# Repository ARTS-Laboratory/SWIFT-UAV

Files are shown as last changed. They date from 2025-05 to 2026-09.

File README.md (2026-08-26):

# Scientific Workhorse for In-flight Field Tests – UAV (SWIFT-UAV)

Repository for the open-source SWIFT-UAV being developed at the University of South Carolina. 

<p align="center">
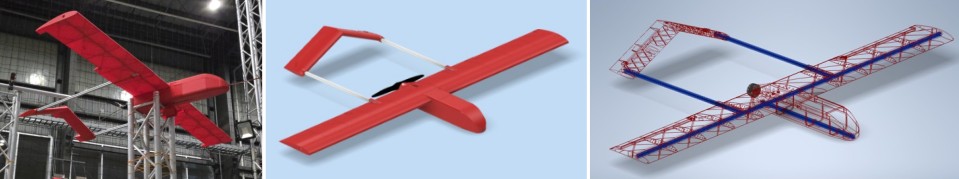
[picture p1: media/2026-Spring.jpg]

</p>
<p align="center">
The SWIFT UAV (Pelican V0.3) in Spring 2026.
</p>

## Licensing and Citation

[][cc-by-sa]

This work is licensed under a
[Creative Commons Attribution-ShareAlike 4.0 International License][cc-by-sa].

[cc-by-sa]: http://creativecommons.org/licenses/by-sa/4.0/
[cc-by-sa-image]: https://licensebuttons.net/l/by-sa/4.0/88x31.png
[cc-by-sa-shield]: https://img.shields.io/badge/License-CC%20BY--SA%204.0-lightgrey.svg

Cite as:

@Misc{ARTSLabSwiftUavScientific,     
  author = {{ARTS-L}ab},  
  howpublished = {GitHub},    
  title  = {SWIFT-UAV: Scientific Workhorse for In-flight Field Tests – UAV},    
  groups = {{ARTS-L}ab},    
  url    = {https://github.com/ARTS-Laboratory/SWIFT-UAV},   
  note        = {Accessed: Month dd, yyyy},   
}

<p align="center">
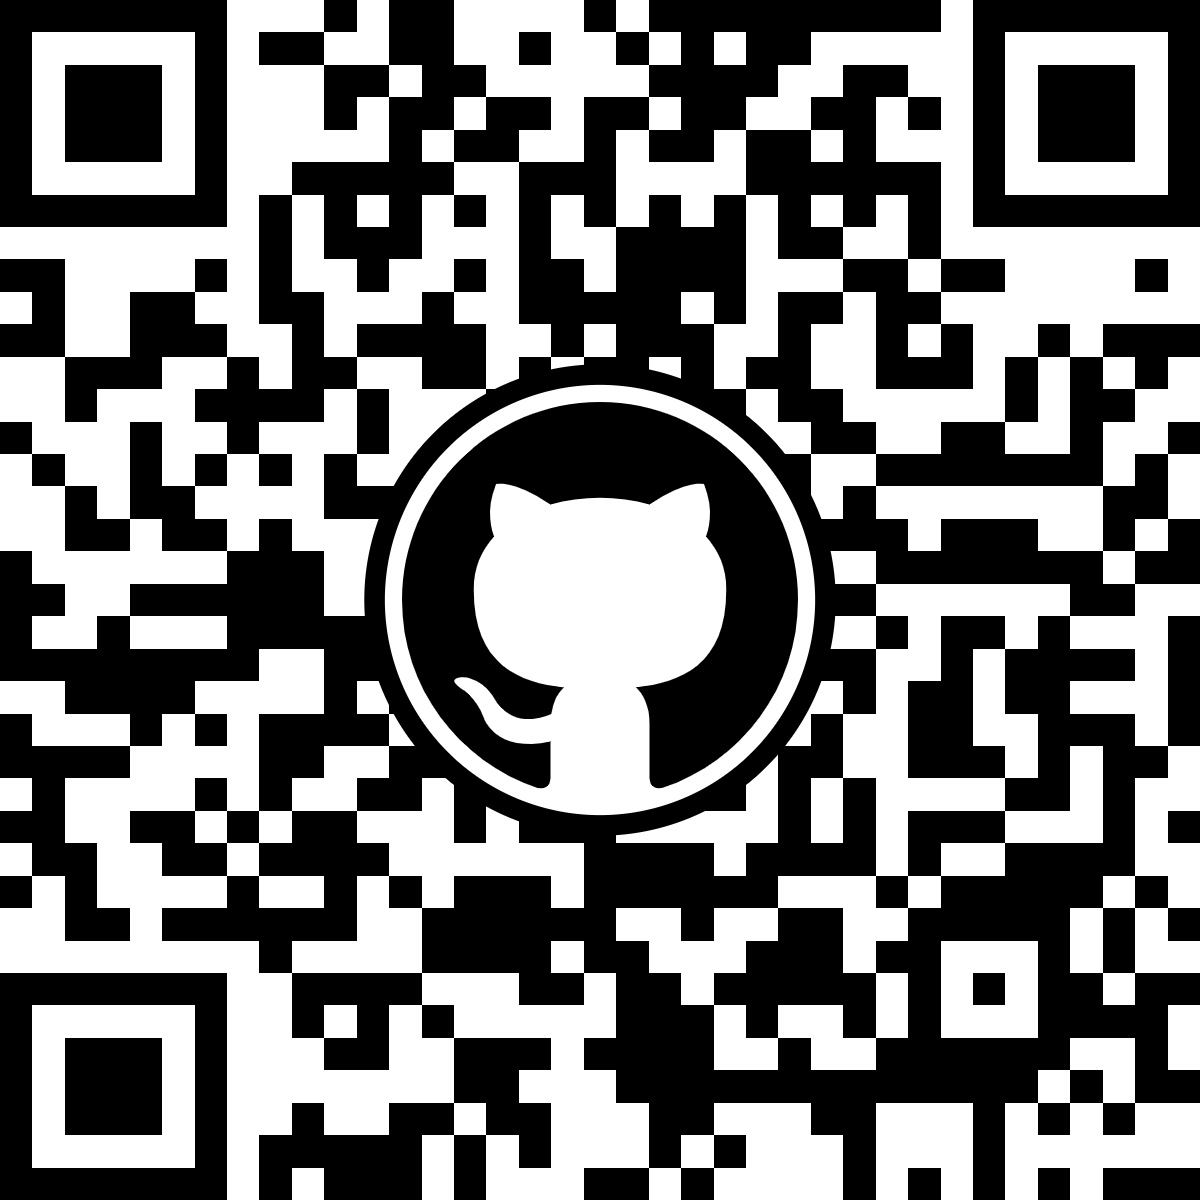
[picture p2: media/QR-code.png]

</p>
<p align="center">
QR code for repo.
</p>

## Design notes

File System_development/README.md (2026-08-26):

# System Development
Variations named after large birds native to South Carolina.

## [Pelican](Pelican)
General base model.

## [Heron](Heron)
Vertical-takeoff-and-landing variant.

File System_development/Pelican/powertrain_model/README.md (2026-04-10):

# Powertrain Model

<p align="center">

</p>
<p align="center">
Pelican V0.1 Powertrain model.
</p>

## v0.1 
Here, we have a model of the v1 version of the SWIFT UAV. It includes the powertrain model i.e.
+ The control system - Closed loop control system with a motion sensor at the Rotor
+ Electronic Speed Controller (ESC)
+ BLDC Motor (X7215 Brushless DC Motor)
+ Propeller - This also includes a few other mechanical components and sensors like the mass and the damper used to represent flight profiles or paths

The model needs to be run with the .mat folder as it contains the input parameters used.

## v0.2
A hybrid lithium-ion and aluminum-air battery powertrain model.

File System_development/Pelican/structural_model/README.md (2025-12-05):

# CAD model

## V0.1
* Developed as a senior design project at USC in the Spring of 2025

## V0.2
* Reworked structure of the senior design project in the summer of 2025
## V0.2.1
* Substantial rework to wing
## V0.2.2
* Substantial rework to fuselage
## V0.2.3
* Squared wing, added 20x20 structural element to fuselage
* Design optimizations for manufacturability
## V0.2.4
* Design optimizations for manufacturability

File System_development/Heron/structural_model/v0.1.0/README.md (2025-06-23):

# V0.1
* Developed as a senior design project at USC in the Spring of 2025

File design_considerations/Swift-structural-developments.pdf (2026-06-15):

## SWIFT UAV

Structural Systems v0.2.3

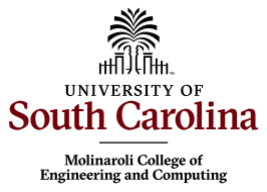
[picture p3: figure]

1

## Design & Manufacturing Progress

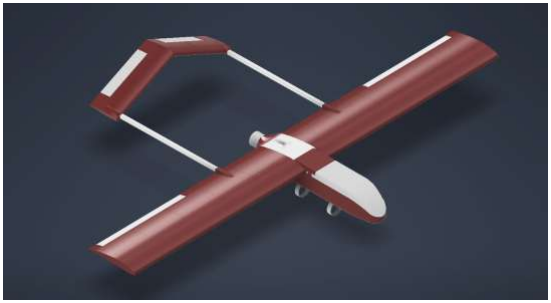
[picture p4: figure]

- Current design iteration
is focused on:
oStructural improvements
oOperational improvements
- Design for manufacturability
- The current (v0.2.3) UAV design is in production
- Initial prints confirm the validity of design changes

## Structural Modifications for Assembly

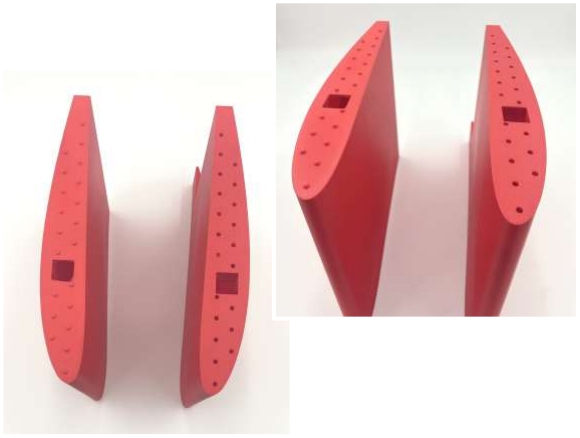
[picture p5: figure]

- Locking nubs have been added
between wing segments
- They provide multiple structural and functional benefits:
- Load Transfer: Enables transfer of shear loads between wing sections
- Improved Assembly: Enables part indexing for easy assembly
- Torsional Stiffness: Increases torsional resistance substantially

## Structural Modifications for Assembly

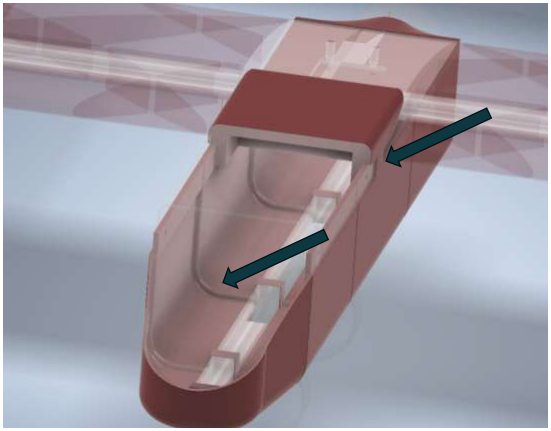
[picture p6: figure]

- Tabs have been added to fuselage
sections
- Provides indexing points to streamline manufacturing and increase joint rigidity
- A slot has been added to the fuselage cover
- Makes for easier and more
ridged assembly
- A 2020 rail has been added in the fuselage to:
- Reinforce the fuselage
- Act as a mounting point for the landing gear
- Act as a hardpoint for payloads

## Avionics Integration

- Preliminary Avionics integration is being conducted in parallel with
the manufacturing
- Ensuring that mounting points and clearances for all the
hardware correct
- The 2020 aluminum bar embedded into the fuselage base also serves:
- A universal mounting interface for avionics trays and payloads.
- And enables easy reconfiguration of internal loadout for missions

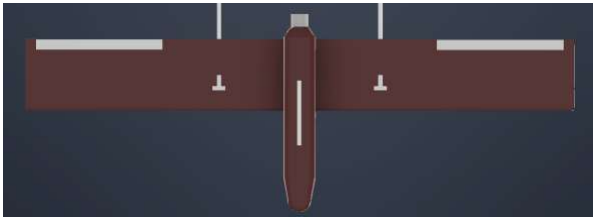
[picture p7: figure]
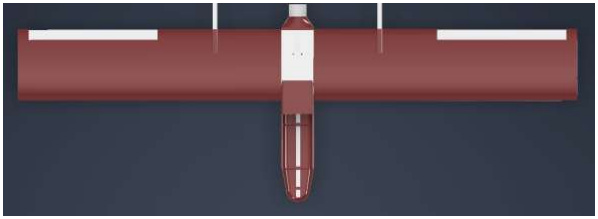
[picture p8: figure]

## Payload Accommodation

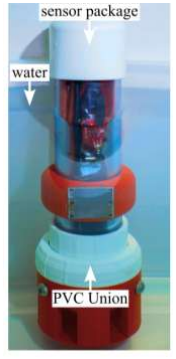
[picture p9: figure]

- A simple pylon structure as added support the mounting
any of the 2" PVC chassis
sensor packages the lab has developed
- Ex. Deployable water quality sensor
- This modularity allows for collaborative research
projects
- external partners can attach their instrumentation without substantially altering the aircraft.
- Future upgrades may include quick-release interfaces.

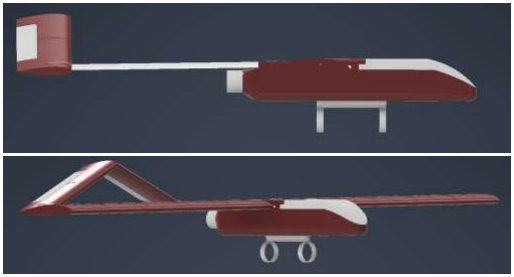
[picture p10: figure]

## Next Steps

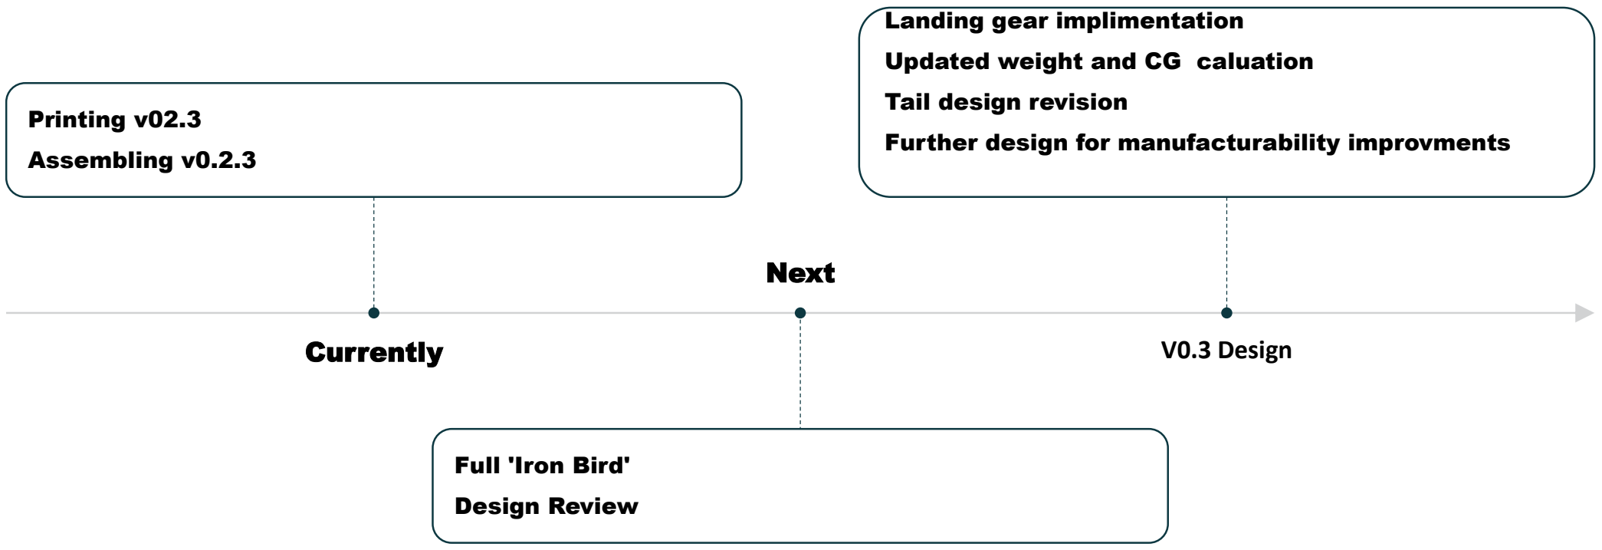
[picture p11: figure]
Currently; Printing v02.3; Assembling v0.2.3; Next; Full 'Iron Bird'; Design Review; V0.3 Design; Landing gear implimentation; Updated weight and CG caluation; Tail design revision; Further design for manufacturability improvments

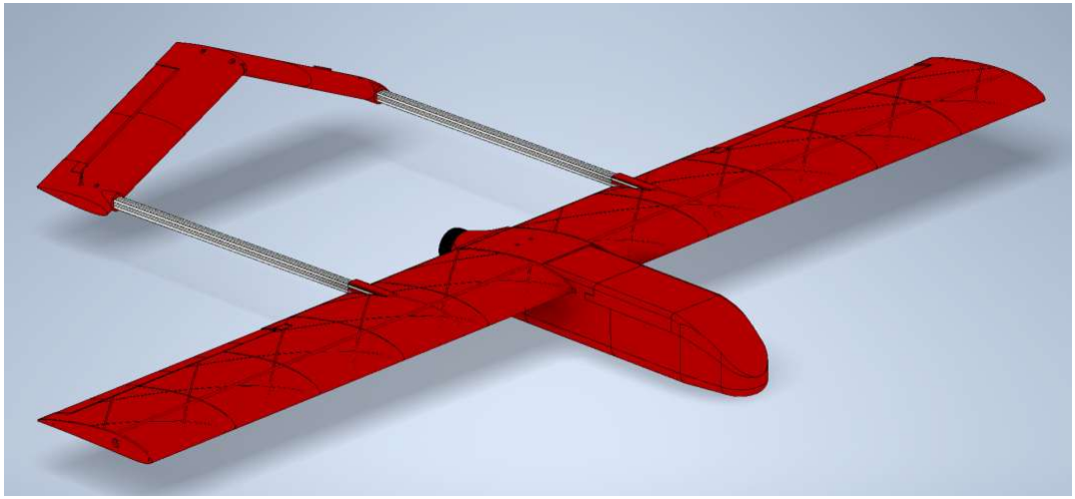
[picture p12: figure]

8

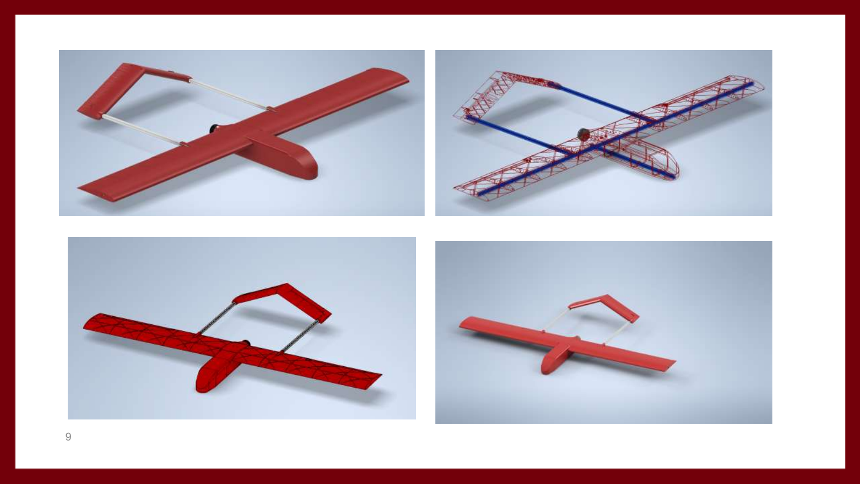
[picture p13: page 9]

9

## Thank You for Your Time

Lab GitHub: github.com/arts-laboratory

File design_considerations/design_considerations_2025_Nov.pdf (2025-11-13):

# MISSION STATMENT

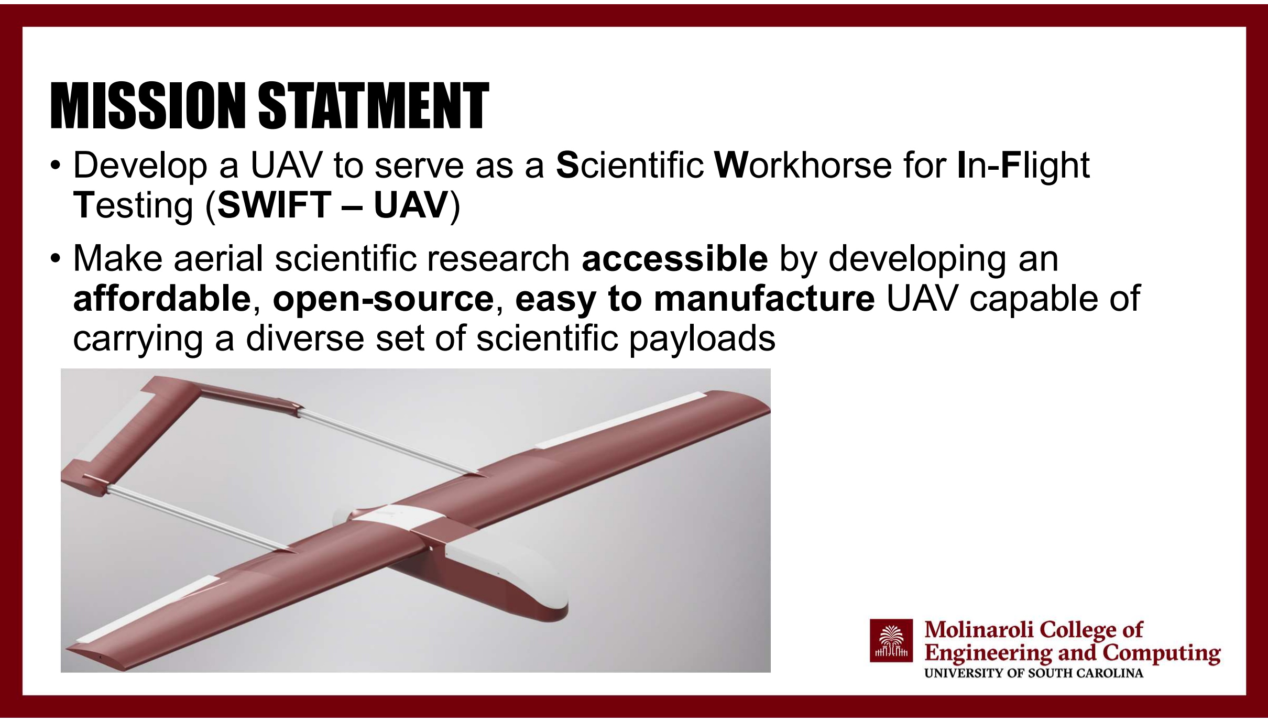
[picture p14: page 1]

- Develop a UAV to serve as a Scientific Workhorse for In-Flight Testing (SWIFT – UAV)
- Make aerial scientific research accessible by developing an affordable, open-source, easy to manufacture UAV capable of carrying a diverse set of scientific payloads

# SWIFT-UAV

Scientific Workhorse for In-flight Field Tests – Unmanned Aerial Vehicle

# OVERVIEW OF DESIGN

- High Wing, twin-boom mono- propeller pusher configuration was selected for its:

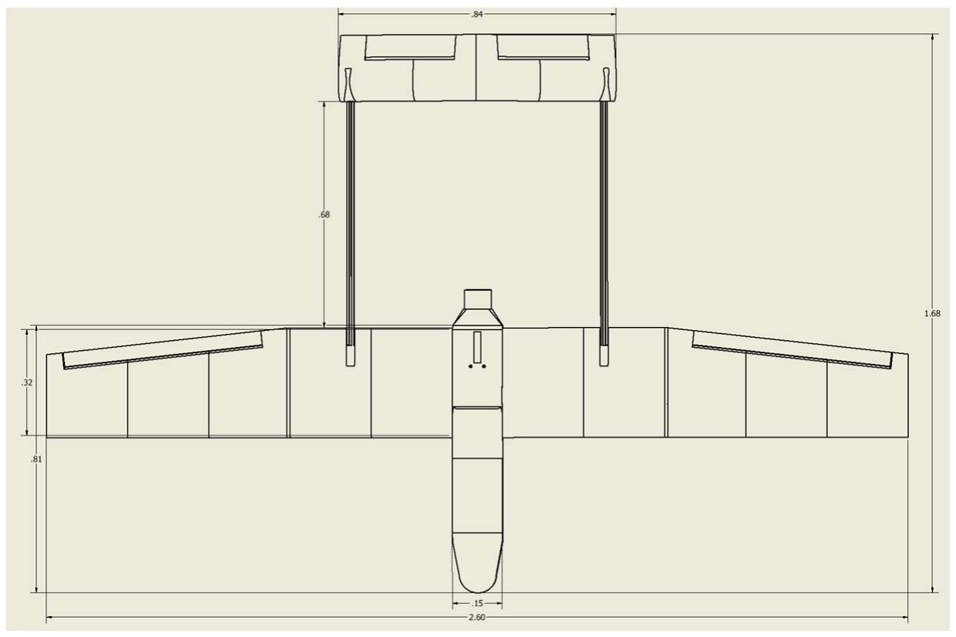
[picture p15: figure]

- aerodynamic stability
- High wing promotes “self-righting” in the roll axis
- aerodynamic efficiency
- No prop-wash over wings
- structural integrity
- “Box” shape enables multiple redundant struts
- built-in safety envelop
- Booms act to protect end users from the propellers path
- ease of payload mounting
- The entire front of the plane is clear to mount almost anything

# TARGETED DESIGN SPECIFICATIONS

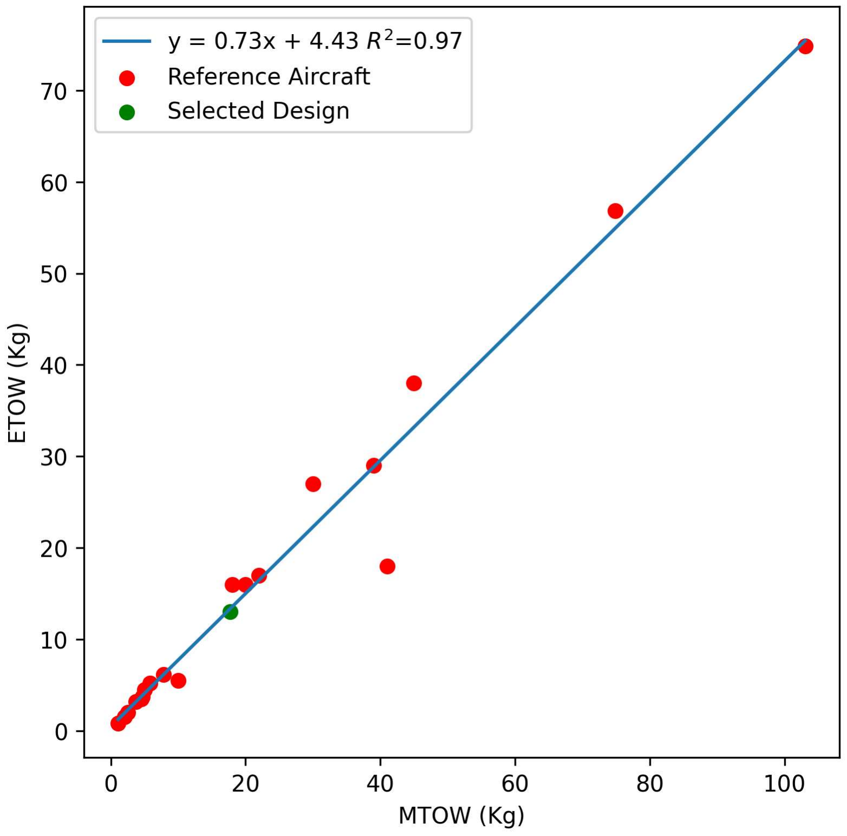
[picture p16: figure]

ETOW | Payload | Cruise | Stakeoff | Range | Endurance
13 Kg | 3 Kg | 20 m/s | 20 m | 5 km | 3 hr
Wing Span | Length | Fuesalge Width Fuesalage Length Airfoil | Root Coord
2.6 m | 1.7 m | 0.15 m | 0.8 m | NACA 2412 | 0.33 m
Tip Coord | Battery Capcity Max TWR | Fuesalage Length Estimated Cost
0.25 m | 10 Ah | | 0.8 1 m | $2,000
- First class estimations of performance done using specifications of similar aircraft in conjunction with classical aerodynamic analysis approaches
- Empirical methods exist to estimate most performance metrics of aircraft
- Conservative estimations

# AERODYNAMICS

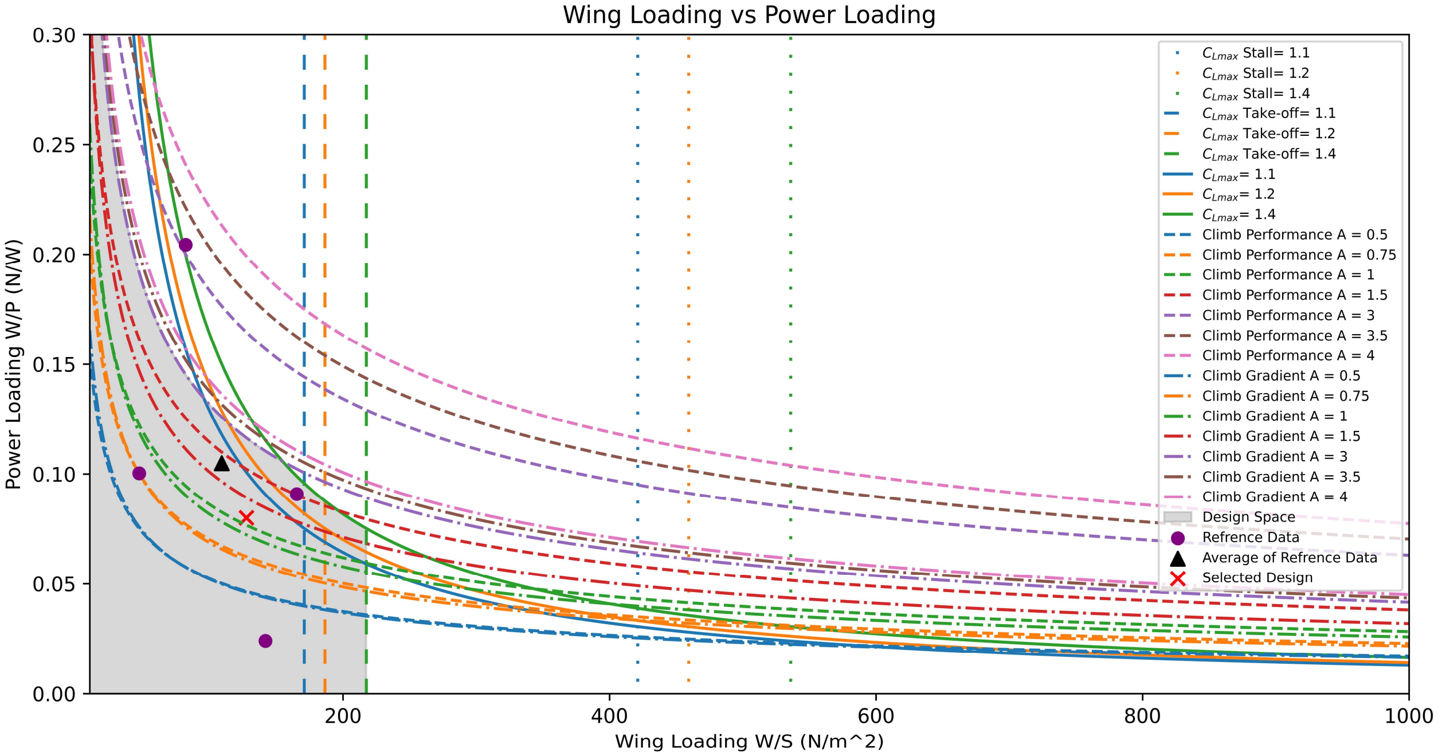
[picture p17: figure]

- Wing first design
- Plane was designed
around the wing
- Classical aerodynamic
wing analysis was
performed to “bound” the
aspect ratio, airfoil, wing length etc.
- Wing Specifications were then chosen to be in line
with reference aircraft

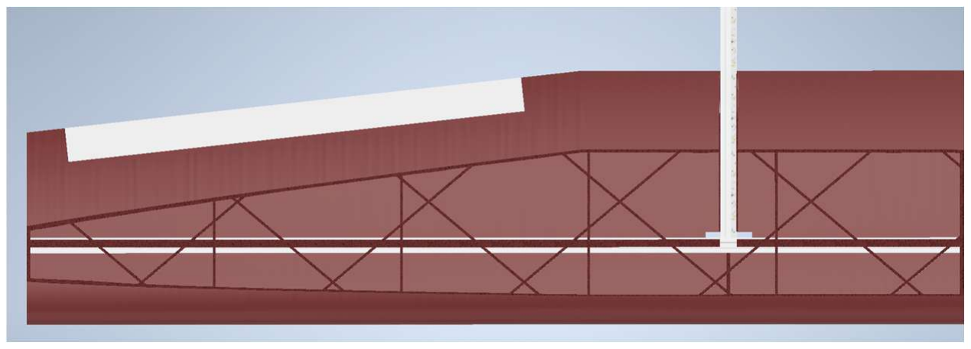
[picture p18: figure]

# STRUCTURAL

- Aluminum extrusion act as spars
- Aluminum is very over-spec relative to the wing loading
- Diagonal Ribs are added to transfer load from wing skin to the central spar
- Skin is very thin walled, 0.8mm
- Since wing has to be printed in section the walls don’t act to carry much shear flow between sections
- Further Design optimization need to better handle torsional loading between sections
- For now, the wing is glued to circumvent this

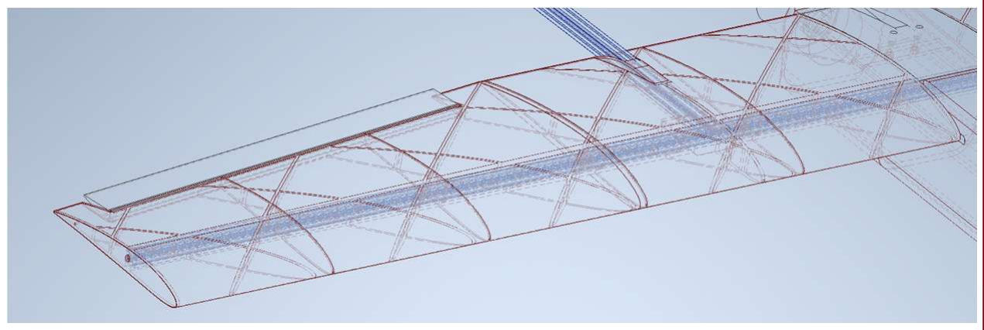
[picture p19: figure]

# MANUFACTURING

- Almost entirely 3D-printed design enable trivial
manufacturing
- In conjunction with the
aluminum extrusion system
used, almost no manual
manufacturing is required
- Cut 20/20

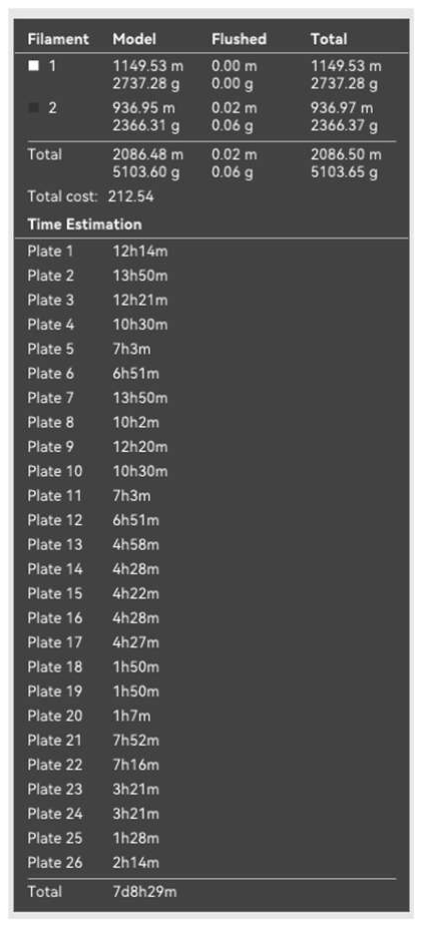
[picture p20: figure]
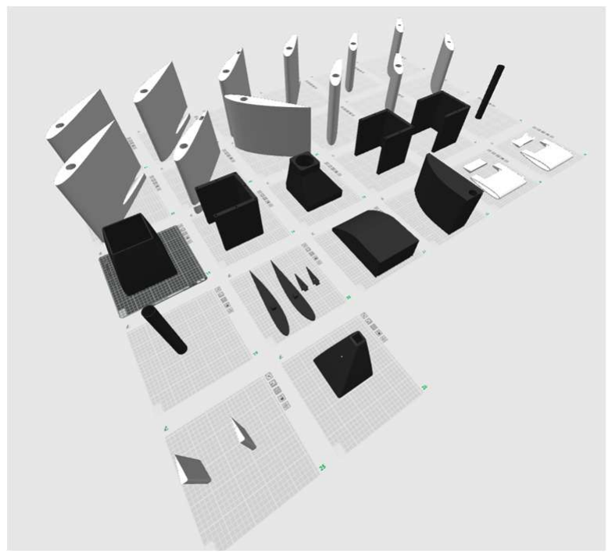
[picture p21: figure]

- Screw/glue parts together | Fig 1: V1.2 in slicer software with estimated print time

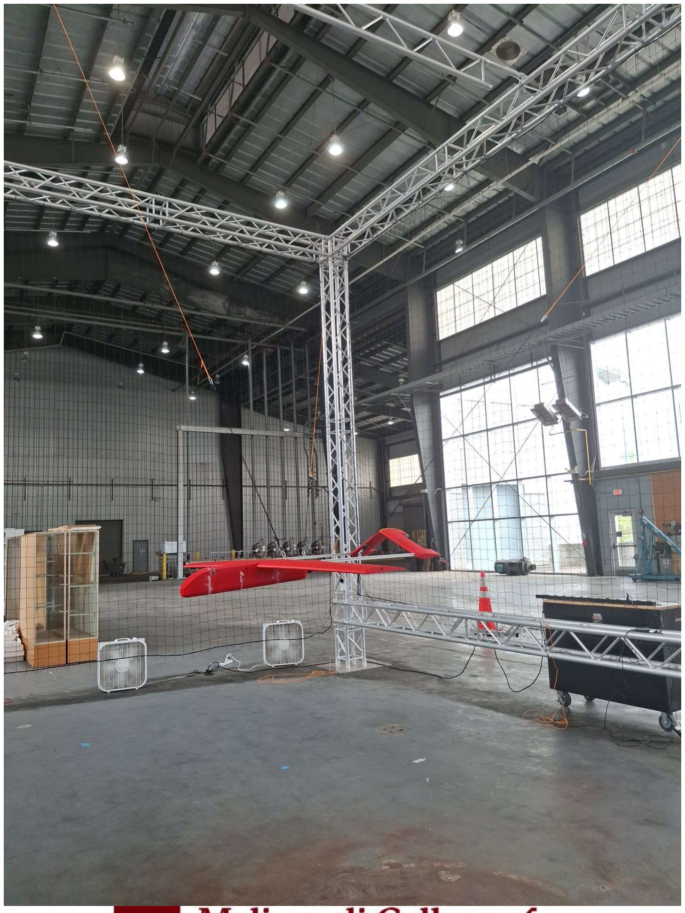
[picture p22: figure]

# “IRON BIRD” TESTING

- Preliminary iron bird
testing will soon be
conducted to validate
electrical systems under
load

# TIMELINE

V1.x
Preliminary
Design

V2.x
Detailed
Design

V3.x Ground
Optimization

V4.x Flight
Tests

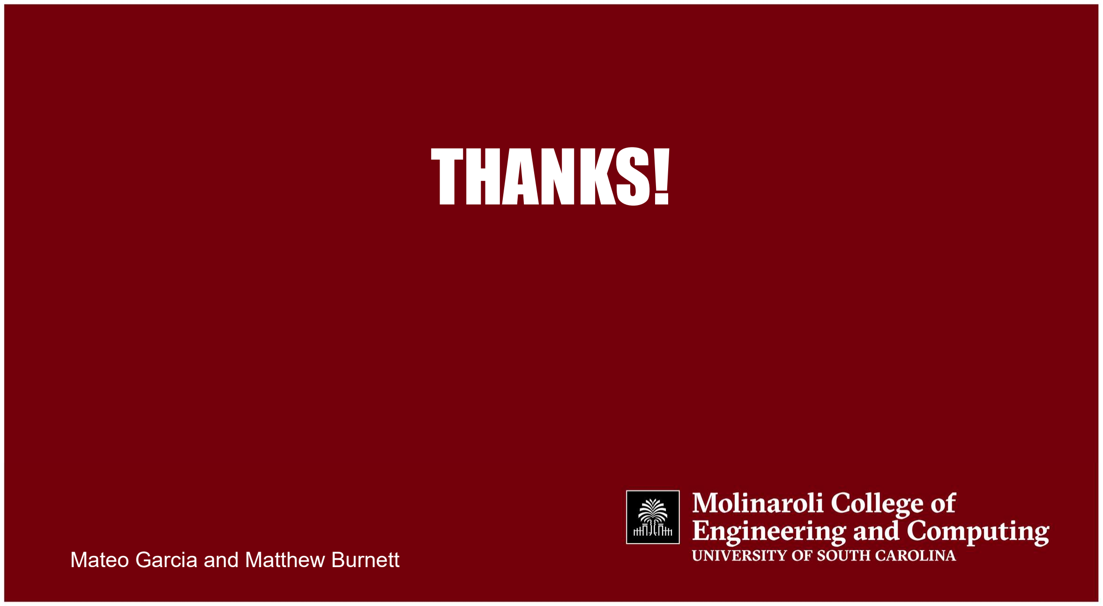
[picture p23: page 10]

# THANKS!

Mateo Garcia and Matthew Burnett

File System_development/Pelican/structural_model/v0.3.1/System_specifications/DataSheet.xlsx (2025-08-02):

Wing |  |  | Frame
wingspan | 2.6 | m | Spar Length | 2.6 | m
Middle Wing span | 0.75 | m | Boom Length (from Wing edge) | 0.715 | m
Wing Root Coord | 0.32 | m | Boom Seperation distance | 0.62 | m
Outer Wing Span | 0.925 | m |  |  | m
Wing Tip Coord | 0.225 | m
Alerion Length | 0.6 | m
Alerion Coord | 0.06 | m
NACA | 2412
 | 0.703125

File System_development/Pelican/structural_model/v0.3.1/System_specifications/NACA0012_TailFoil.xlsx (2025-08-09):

mm
y | x
0.378 | 200
0.40257 | 199.88322
0.4761 | 199.53316
0.59814 | 198.95064
0.76785 | 198.137
0.98412 | 197.09418
1.24557 | 195.82458
1.55055 | 194.33118
1.89714 | 192.61746
2.28324 | 190.68744
2.70651 | 188.5456
3.16455 | 186.19698
3.65469 | 183.64702
4.17429 | 180.9017
4.72053 | 177.96744
5.29059 | 174.85108
5.88153 | 171.5599
6.49041 | 168.10158
7.11426 | 164.48422
7.75011 | 160.71626
8.39484 | 156.80648
9.04545 | 152.76404
9.69882 | 148.59834
10.35174 | 144.31916
11.001 | 139.93646
11.64327 | 135.4605
12.27522 | 130.9017
12.89334 | 126.27074
13.49406 | 121.57842
14.07372 | 116.83572
14.62857 | 112.05366
15.15483 | 107.24348
15.6486 | 102.41638
16.10598 | 97.58362
16.52307 | 92.75652
16.896 | 87.94634
17.22099 | 83.1643
17.49435 | 78.42158
17.71257 | 73.72926
17.87241 | 69.0983
17.97084 | 64.53952
18.00516 | 60.06354
17.97306 | 55.68084
17.87265 | 51.40166
17.70243 | 47.23598
17.46144 | 43.19352
17.1492 | 39.28374
16.76568 | 35.51578
16.31145 | 31.89842
15.78753 | 28.4401
15.19539 | 25.14892
14.53701 | 22.03256
13.81467 | 19.0983
13.03113 | 16.35298
12.1893 | 13.80304
11.29242 | 11.4544
10.34376 | 9.31256
9.34677 | 7.38254
8.30481 | 5.66882
7.22118 | 4.17542
6.099 | 2.90582
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

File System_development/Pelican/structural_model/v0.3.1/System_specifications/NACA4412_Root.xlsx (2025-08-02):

mm
y | x
0.429 | -330
4.851 | -313.5
8.943 | -297
16.137 | -264
22.077 | -231
26.862 | -198
30.327 | -165
32.34 | -132
32.208 | -99
31.053 | -82.5
29.04 | -66
26.037 | -49.5
21.747 | -33
19.008 | -24.75
15.609 | -16.5
11.187 | -8.25
8.052 | -4.125
0 | 0
-4.719 | -4.125
-6.435 | -8.25
-8.217 | -16.5
-9.042 | -24.75
-9.438 | -33
-9.504 | -49.5
-9.042 | -66
-8.25 | -82.5
-7.458 | -99
-5.94 | -132
-4.62 | -165
-3.3 | -198
-2.145 | -231
-1.287 | -264
-0.726 | -297
-0.528 | -313.5
-0.429 | -330

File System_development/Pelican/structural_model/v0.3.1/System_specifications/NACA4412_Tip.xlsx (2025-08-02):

mm
y | x
0.325 | -250
3.675 | -237.5
6.775 | -225
12.225 | -200
16.725 | -175
20.35 | -150
22.975 | -125
24.5 | -100
24.4 | -75
23.525 | -62.5
22 | -50
19.725 | -37.5
16.475 | -25
14.4 | -18.75
11.825 | -12.5
8.475 | -6.25
6.1 | -3.125
0 | 0
-3.575 | -3.125
-4.875 | -6.25
-6.225 | -12.5
-6.85 | -18.75
-7.15 | -25
-7.2 | -37.5
-6.85 | -50
-6.25 | -62.5
-5.65 | -75
-4.5 | -100
-3.5 | -125
-2.5 | -150
-1.625 | -175
-0.975 | -200
-0.55 | -225
-0.4 | -237.5
-0.325 | -250

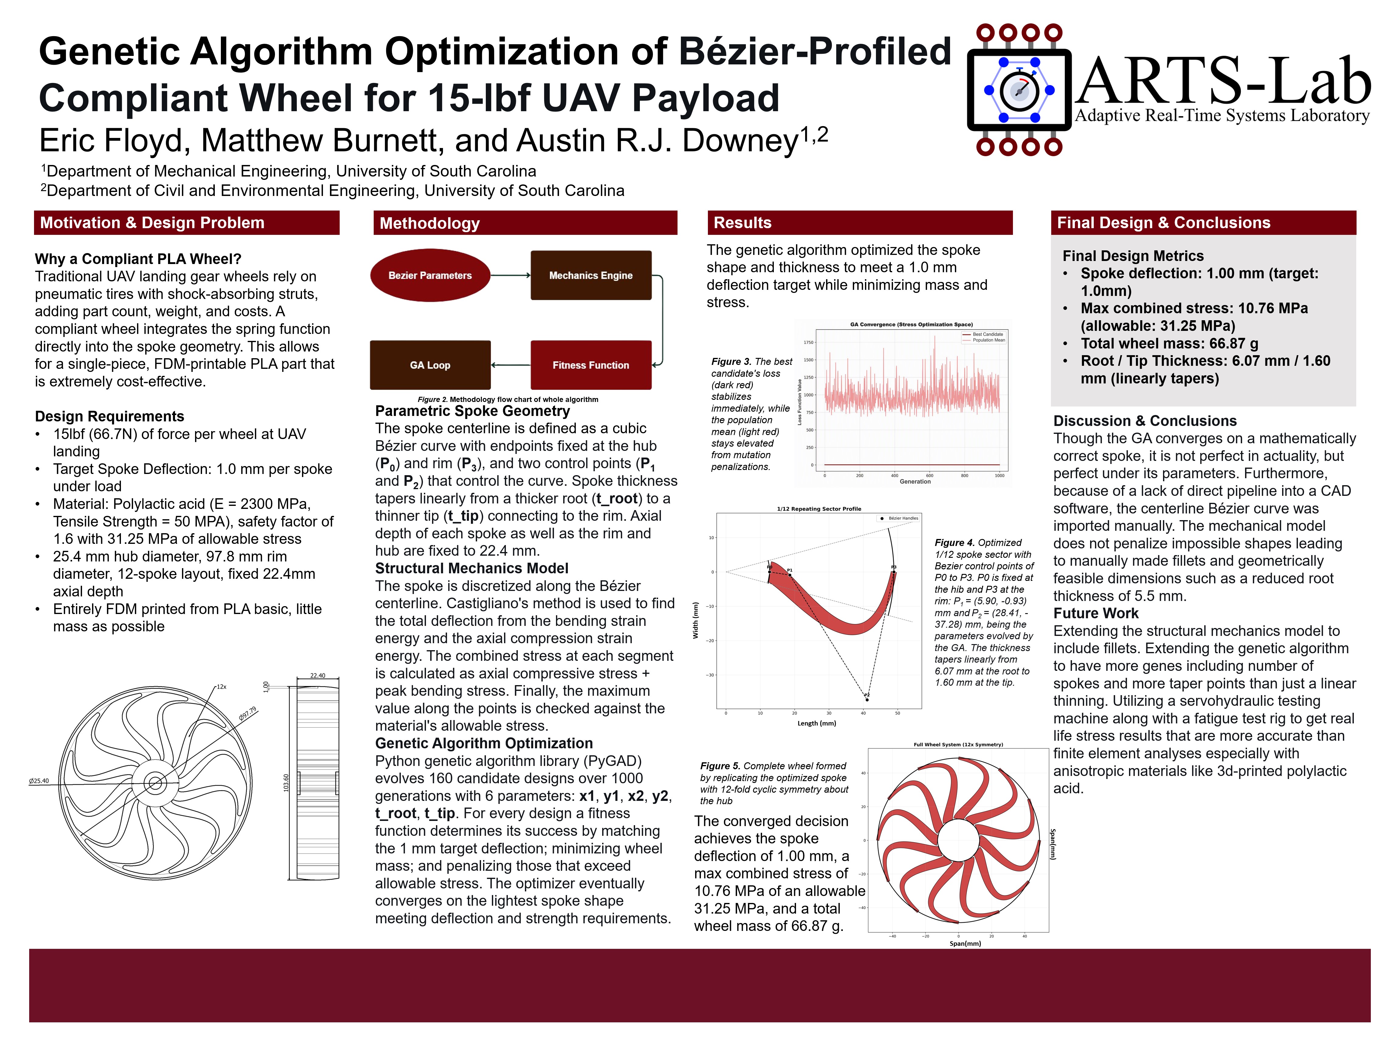
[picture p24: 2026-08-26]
System_development/Pelican/structural_model/v0.3.1/Parts/Landing Gear/Posters and Code/ga_wheel_poster.jpg

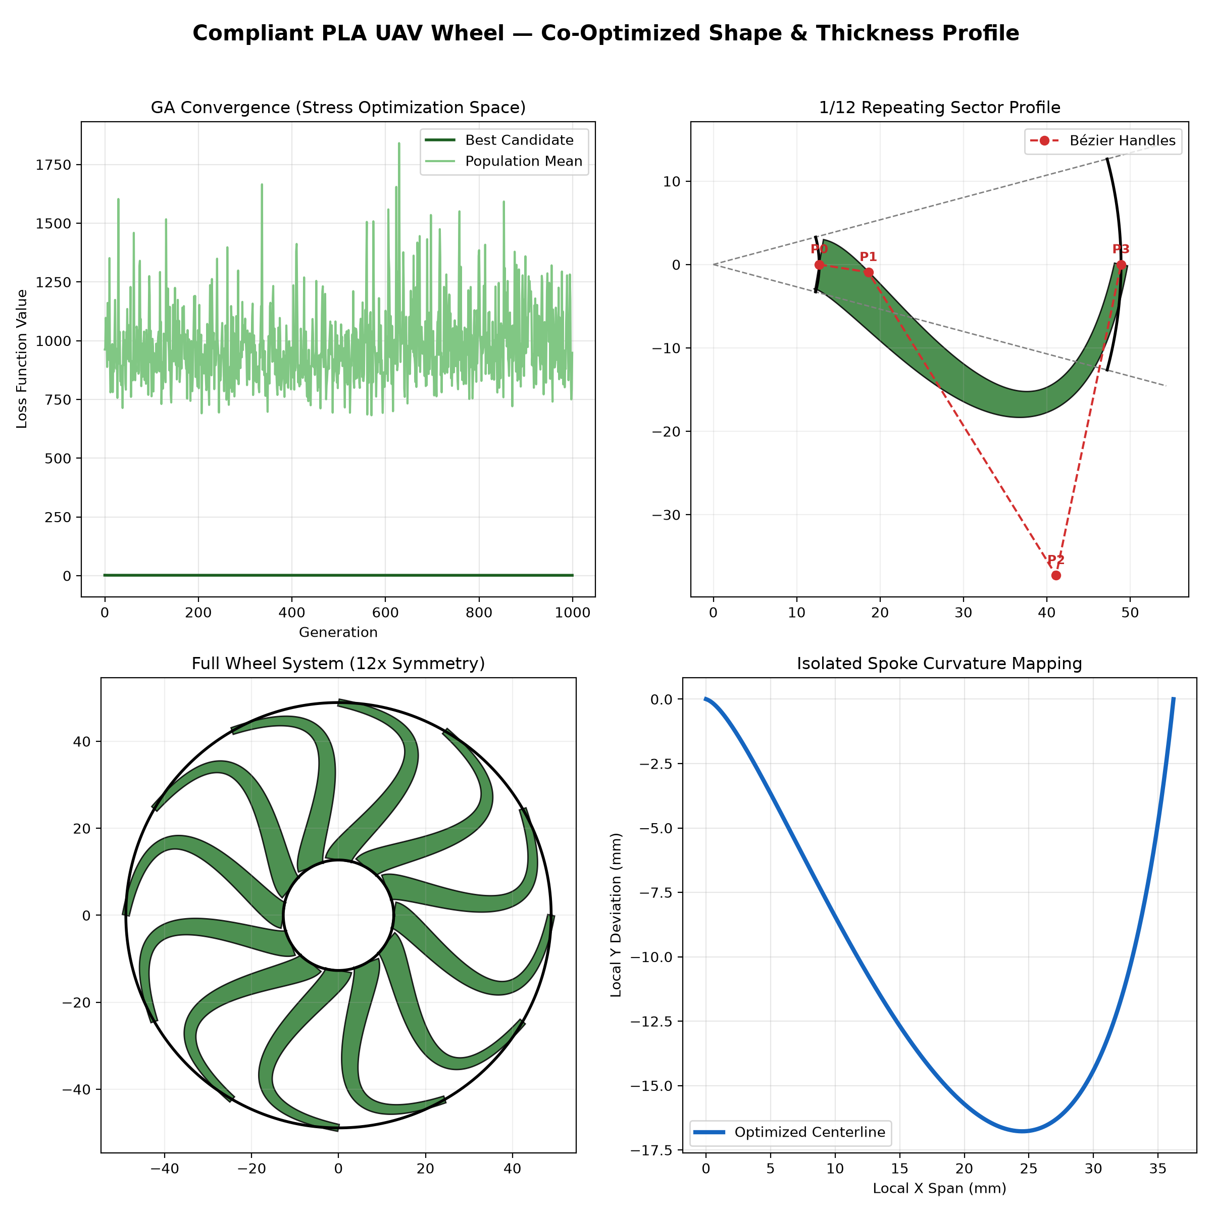
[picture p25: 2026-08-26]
System_development/Pelican/structural_model/v0.3.1/Parts/Landing Gear/Posters and Code/poster_summary.png

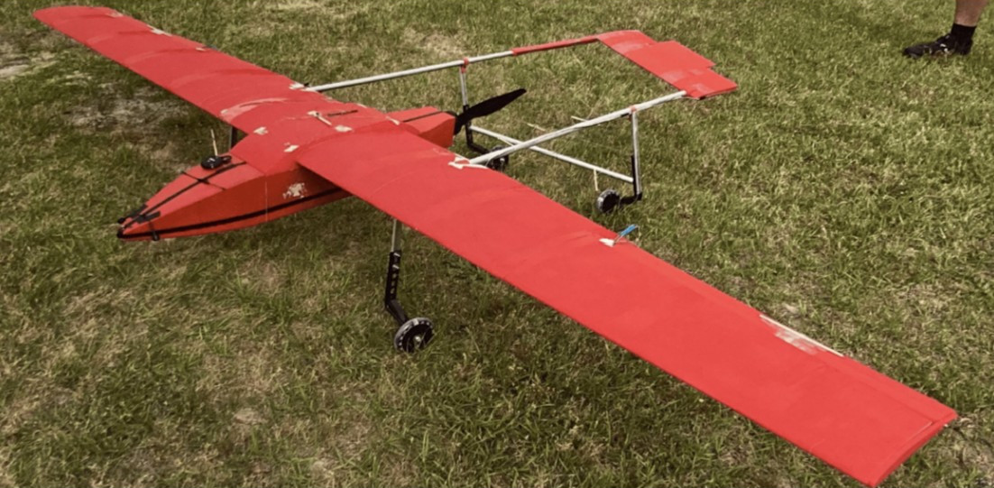
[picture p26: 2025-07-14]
media/2025-Spring.jpg

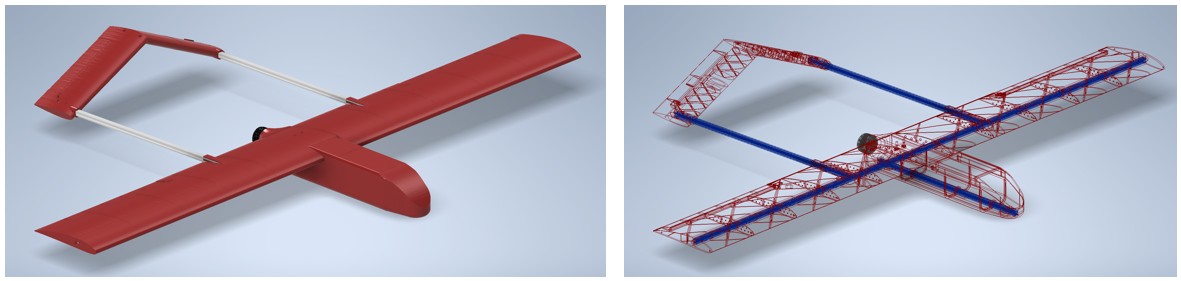
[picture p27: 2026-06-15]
media/2026-Spring-2.jpg

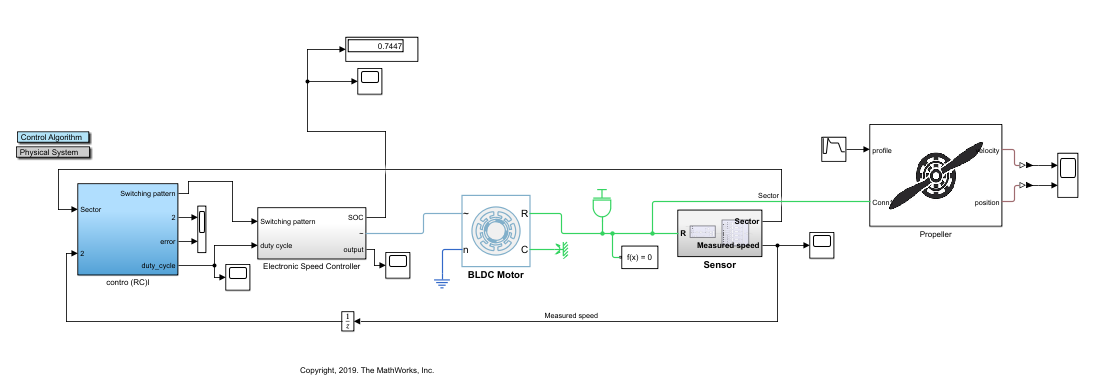
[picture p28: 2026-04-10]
System_development/Pelican/powertrain_model/media/v0.1.png

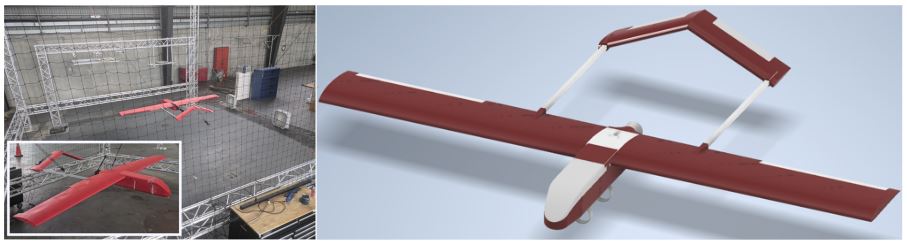
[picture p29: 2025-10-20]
media/2025-Fall.jpg

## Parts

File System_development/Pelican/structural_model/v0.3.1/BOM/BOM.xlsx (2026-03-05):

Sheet: Needed
Needed BOM omits parts the Iron bird will never need or parts that can readily be used for both, (video transmision for example)
 | Name | Quanitity | Price | Total Price | Source | Description + Specificers + Manufactuerer Name
 | T-Slot Nut | 4 | $1.60 | $6.40 | Link (https://www.aliexpress.us/item/3256808146819631.html?src=google) | Running Low
 | Motor | 1 | $189.00 | $189.00 | Link (https://tinyurl.com/mvcsa2zp)
 | Propeller | 2 | $79.00 | $158.00 | Link (https://mad-motor.com/products/21-inch-carbon-fiber-propeller-1pc?VariantsId=10269) | Spare Required
 | Pitot | 1 | $49.99 | $49.99 | Link (https://tinyurl.com/4dfjr2ct)
 | GPS | 1 | $43.99 | $43.99 | Link (https://tinyurl.com/4ffmuvcu)
 | LiPo 6s Battery (two pack) | 1 | $429.99 | $306.00 | Link (https://zeeebattery.com/collections/zeee-6s-lipo-battery/products/zeee-6s-lipo-battery-10000mah-22-2v-120c-ec5) | Currently on sale for 306
 | Voltage Step Down | 1 | $24.99 | $24.99 | Link (https://www.getfpv.com/mateksys-12s-pro-bec-9-55v-to-5v-8v-12v-5a.html) | For servos
 | ESC | 1 | $65.00 | $65.00 | Link (https://tinyurl.com/y4ey9ss9) | DRONE CAN
 | PixHawk 6x Flight Controller | 1 | $280.00 | $280.00 | Link (https://holybro.com/products/pixhawk-6x?variant=44390763430077)
 | KST DS215MG Servo (4pack) | 1 | $156.02 | $156.02 | Link (https://www.aliexpress.us/item/3256801472318919.html?src=google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)
 | Telemetry Radio | 1 | $175.00 | $175.00 | Link (https://tinyurl.com/mvby7523)
 | Remote ID Module | 1 | $19.99 | $19.99 | Link (https://holybro.com/products/remote-id?variant=43034167312573) | FAA Required | w/o case
 | Wire Extensions | 5 | $12.57 | $62.85 | Link (https://tinyurl.com/3ffam8a5)
 | Total |  |  | $1537.23

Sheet: Detailed
Name | Quanitity | Price | Total Price | Source | Description + Specificers + Manufactuerer Name
Fuselage | 1 | $0.00 | $0.00 | 3D printed
Front Cover | 1 | $0.00 | $0.00 | 3D printed
Wings | 1 | $0.00 | $0.00 | 3D printed
Tail | 1 | $0.00 | $0.00 | 3D printed
Aluminum 20x20 | 6 m | $0.00 | $57.90 | Link (https://www.grainger.com/product/80-20-T-Slot-Framing-Extrusion-Square-16U247) | Can order at (https://www.vevor.com/aluminum-extrusion-linear-rail-c_44271/10pcs-78-7-in-2000mm-t-slot-2020-aluminum-extrusion-anodized-linear-rail-p_010564031144)
M5 |  |  | $0.00
T-Slot Nut |  | $0.00 | $1.60 | Link (https://www.aliexpress.us/item/3256808146819631.html?src=google)
T-Plate | 3 | $9.68 | $29.04 | Link (https://tinyurl.com/msezv4u3)
PixHawk 6x Flight Controller | 1 | $280.00 | $280.00 | Link (https://holybro.com/products/pixhawk-6x?variant=44390763430077) |  | 0
Motor | 1 | $189.00 | $189.00 | Link (https://tinyurl.com/mvcsa2zp)
Propeller | 2 | $79.00 | $158.00 | Link (https://mad-motor.com/products/21-inch-carbon-fiber-propeller-1pc?VariantsId=10269) | Spare Required
Pitot | 1 | $49.99 | $49.99 | Link (https://tinyurl.com/4dfjr2ct)
VTX | 1 | $33.99 | $33.99 | Link (https://www.ebay.com/itm/167641152972)
GPS | 1 | $43.99 | $43.99 | Link (https://tinyurl.com/4ffmuvcu)
LiPo 6s Battery (two pack) | 1 | $429.99 | $429.99 | Link (https://zeeebattery.com/collections/zeee-6s-lipo-battery/products/zeee-6s-lipo-battery-10000mah-22-2v-120c-ec5) | * currently on sale for 306
Voltage Step Down | 1 | $24.99 | $24.99 | Link (https://www.getfpv.com/mateksys-12s-pro-bec-9-55v-to-5v-8v-12v-5a.html)
ESC | 1 | $65.00 | $65.00 | Link (https://tinyurl.com/y4ey9ss9)
KST DS215MG | 4 | $22.99 | $91.96 | Link (https://www.horizonhobby.com/product/SPMSH3055.html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)
Telemetry Radio | 1 | $175.00 | $175.00 | Link (https://tinyurl.com/mvby7523)
Remote ID Module | 1 | $19.99 | $19.99 | Link (https://holybro.com/products/remote-id?variant=43034167312573)
TX | 1 | $209.99 | $209.99 | Link (https://holybro.com/products/radiomaster-tx16s?variant=42712982225085&country=US&currency=USD)
RX | 1 | $64.99 | $64.99 | Link (https://www.getfpv.com/radios/receiver-transmitter-combos/happymodel-expresslrs-es900tx-es900rx-long-range-combo.html)
Wire Extensions | 5 | $12.57 | $62.85 | Link (https://tinyurl.com/3ffam8a5)
M6 |  | $0.00 | $0.00
Total |  |  | $1988.27
*separate into must haves to fly and extra credit

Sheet: Battery Calcs
Number of Cells | Lift Force (N) |  | CL |  |  | AOA (degrees) | CL | Lift (N) | Speed (m/s) | Lift Force (N)
1893987 | 86.1 | 1.58% | 0.409 | 1.71% |  | 0 | 0.395 | 83.2 | (AOA 3)
3632193 | 84.74 | 1.56% | 0.402 | 1.49% |  | 1 |  |  | 30 | 191.1
6292121 | 83.42 |  | 0.396 |  |  | 2 |  |  | 25 | 131.77
 |  |  |  |  |  | 3 | 0.396 | 83.3
 |  |  |  |  |  | 4 |  |  | (AOA 2)
 |  |  |  |  |  | 5 | 0.404 | 85.1 | 25 | 131.82
Variations |  | Results
AOA (deg) | Flight Velocity (m/s) | CL | CD | CM | Lift Force (N) | Drag Force (N)
0 | 20 | 0.4024 | 0.0469 | -0.0619 | 84.791 | 9.882
2 | 20 | 0.4046 | 0.0469 | -0.0623 | 85.239 | 9.878
2 | 25 | 0.4004 | 0.0456 | -0.0609 | 131.826 | 14.999
3 | 20 | 0.3956 | 0.0463 | -0.0603 | 83.346 | 9.758
3 | 25 | 0.4003 | 0.0456 | -0.061 | 131.776 | 15.022
3 | 30 | 0.403 | 0.0451 | -0.0614 | 191.072 | 21.39 |  | ~ 20kg of lift
5 | 20 | 0.4039 | 0.047 | -0.0623 | 85.095 | 9.893
Engine sizing
 |  | Assume
 |  |  |  | 20kgf lift
 |  |  |  | 3 kgf drag | Very conservative estimate (will likley be closer to 2kgf)
 |  |  |  | 6.666666667 | L/D ratio | (cesna is 9 for context)
 | Config 1 |  |  |  |  | Config 3 |  |  |  | Config 5
 | 10S 19x10 |  |  |  |  | 10S 20x10 |  |  |  | 10S 21x10 |  |  | Clearly 21x10 prop
 | Cruise @ | 50% | 11 Amps |  |  | Cruise @ | 50% | 11.74 |  | Cruise @ | 45% | 8 Amps
Max thrust (TWR) |  | 0.535 |  |  | Max thrust (TWR) |  | 0.58375 |  | Max thrust (TWR) |  | 0.665
 | Config 2 |  |  |  |  | Config 4 |  |  |  | Config 6
 | 12S 19x10 |  |  |  |  | 12S 20x10 |  |  |  | 12S 21x10
 | Cruise @ | 45% | 9.1 Amps |  |  | Cruise @ | 45% | 10.1 Amps |  | Cruise @ | 40% | 8.6 Amps
Max thrust (TWR) |  | 0.62 |  |  | Max thrust (TWR) |  | 0.6588 |  | Max thrust (TWR) |  | 0.74
Battey sizing
Target 1hr cruise
assume 120% cruise capacity for take of and landing use
Config 5 10S |  | Battery weight
9.6 | Ah
Config 6 12S |  | Battery weight
10.32 | Ah | 1Kg
 |  |  | https://zeeebattery.com/collections/zeee-6s-lipo-battery/products/zeee-6s-lipo-battery-10000mah-22-2v-120c-ec5

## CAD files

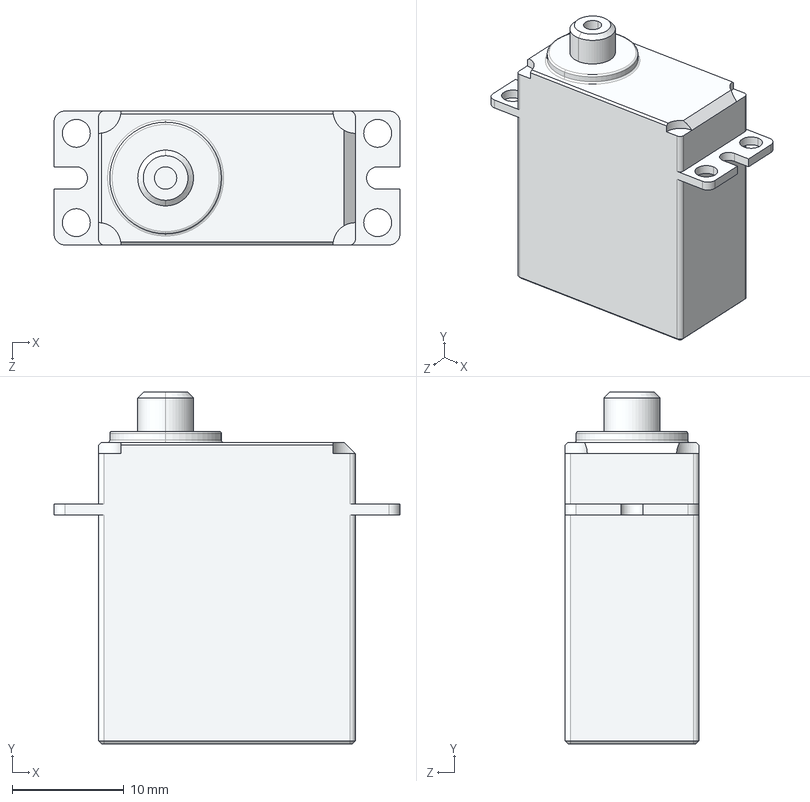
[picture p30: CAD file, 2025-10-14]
System_development/Pelican/structural_model/v0.3.1/Avionics/kst-ds215mg-servo-1.snapshot.4/KST_DS215MG.STEP
31.0 x 31.5 x 12.0 mm

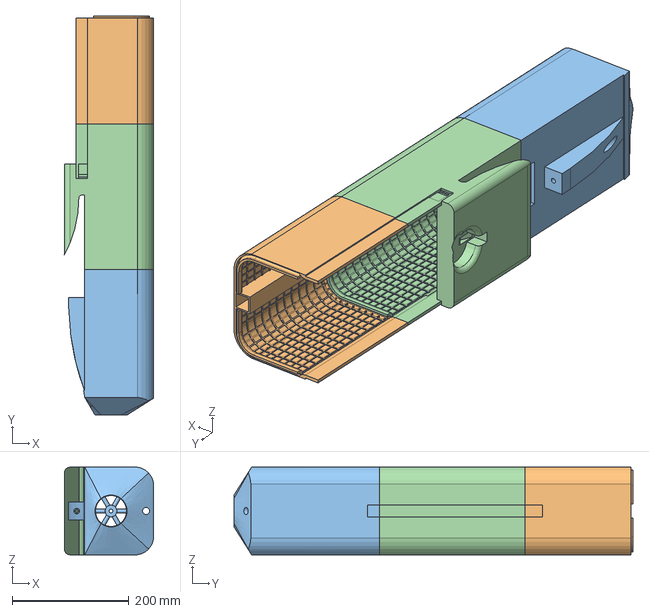
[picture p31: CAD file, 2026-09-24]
System_development/Pelican/structural_model/v0.3.1/Manufacturing/FuselageV3.stp
153.0 x 683.2 x 150.0 mm

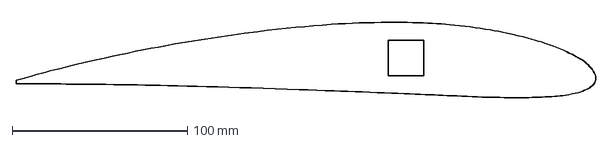
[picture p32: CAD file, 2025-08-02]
System_development/Pelican/structural_model/v0.3.1/Parts/RefrenceSketches/WingRoot.dxf
330.9 x 43.0 mm

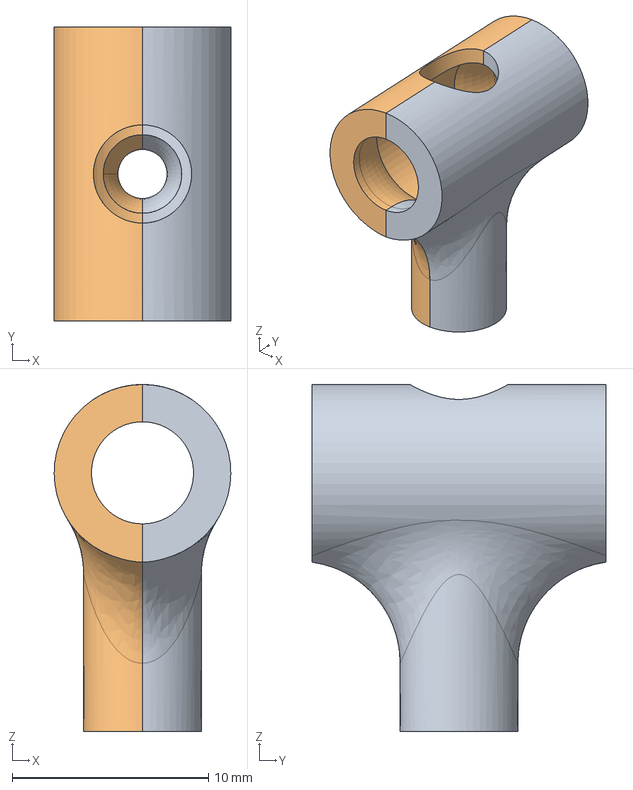
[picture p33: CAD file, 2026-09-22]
System_development/Pelican/structural_model/v0.3.1/Manufacturing/TJoint.stp
9.00 x 15.0 x 17.7 mm

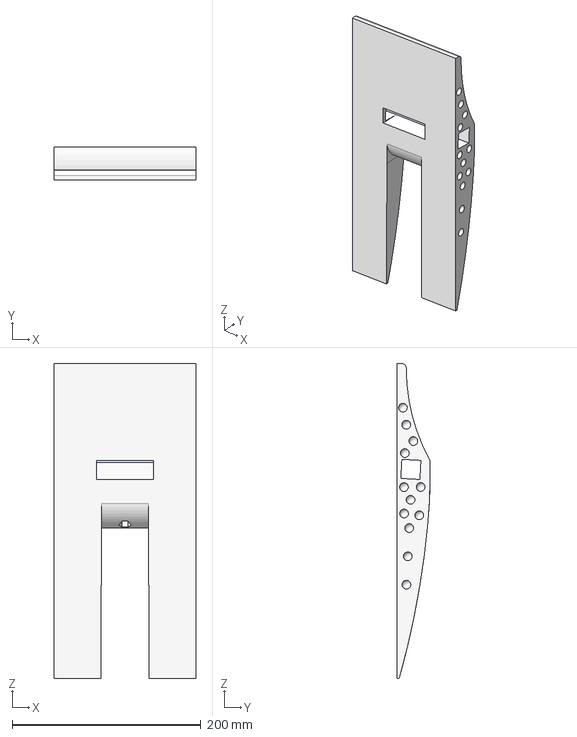
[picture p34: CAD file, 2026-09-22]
System_development/Pelican/structural_model/v0.3.1/Manufacturing/WingBox_v2.stp
150.0 x 35.1 x 333.6 mm

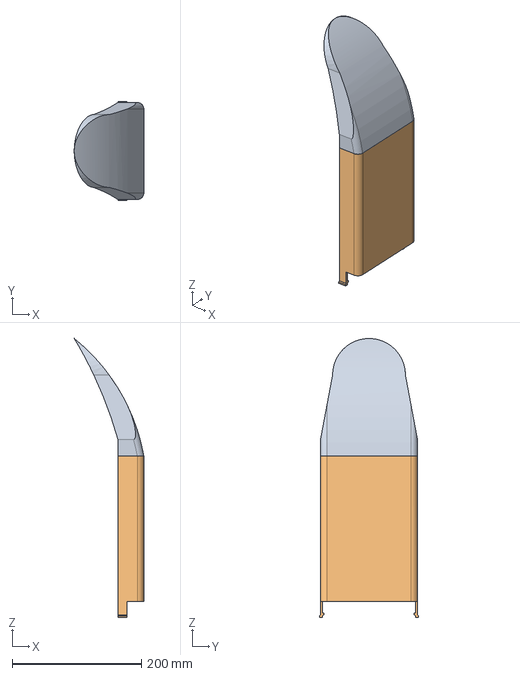
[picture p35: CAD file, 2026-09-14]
System_development/Pelican/structural_model/v0.3.1/Manufacturing/FrontCover.stp
107.6 x 153.0 x 431.2 mm

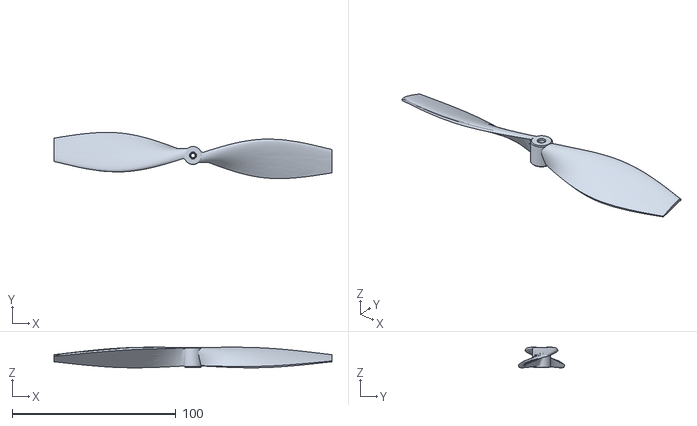
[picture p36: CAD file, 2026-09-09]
System_development/Heron/structural_model/v0.1.0/Prop.stl
170.0 x 28.2 x 12.6

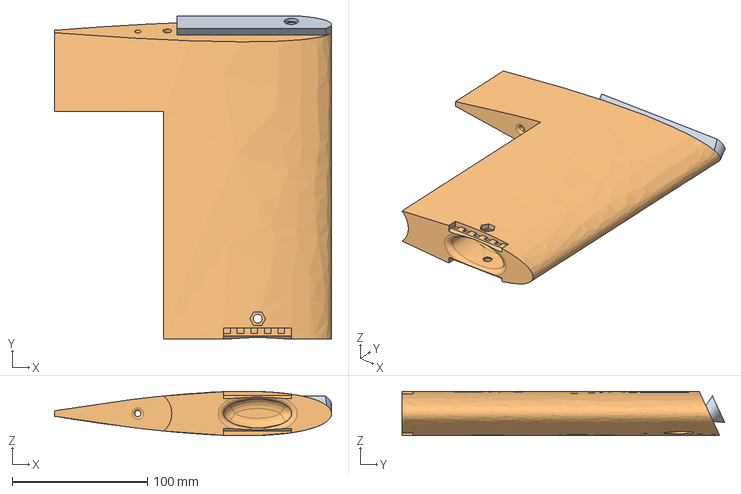
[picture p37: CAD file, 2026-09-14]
System_development/Pelican/structural_model/v0.3.1/Manufacturing/Male_tail_Connector.stp
204.5 x 238.2 x 32.8 mm
connector
Male_Tail_Female_Connector

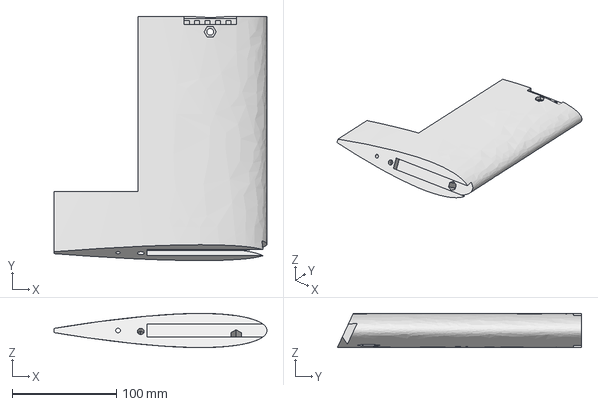
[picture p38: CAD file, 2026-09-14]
System_development/Pelican/structural_model/v0.3.1/Manufacturing/Female_Tail_Female_Connector.stp
204.5 x 234.6 x 32.9 mm

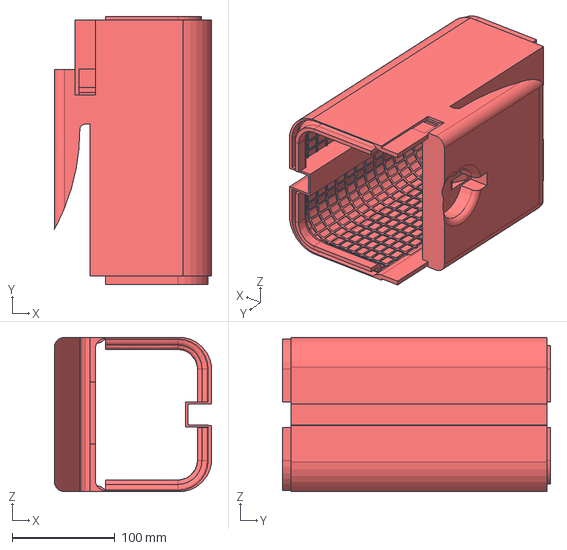
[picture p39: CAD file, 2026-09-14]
System_development/Pelican/structural_model/v0.3.1/Manufacturing/FuselageV2_wingboxarea.stp
153.0 x 260.5 x 150.0 mm

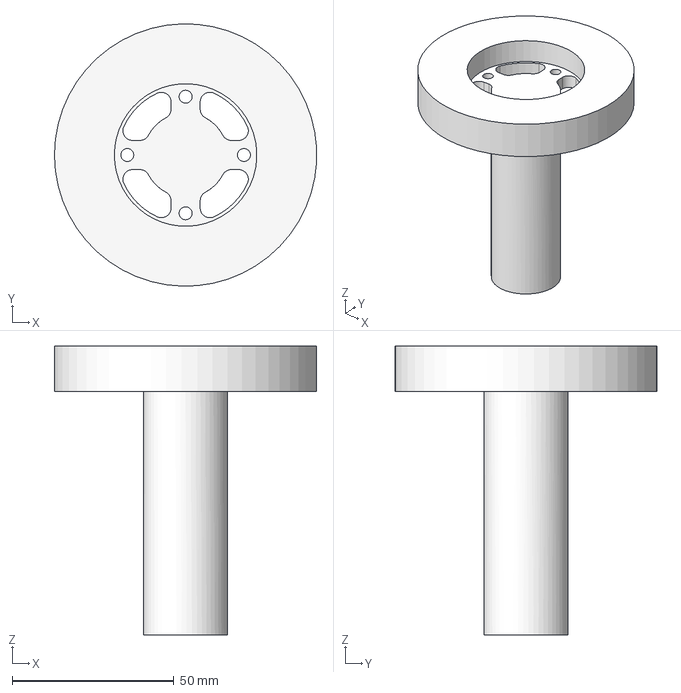
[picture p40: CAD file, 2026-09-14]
System_development/Pelican/structural_model/v0.3.1/Manufacturing/MotorHousingV2.stp
80.9 x 81.0 x 89.2 mm

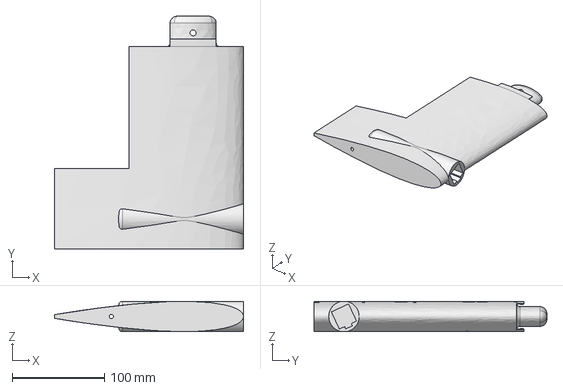
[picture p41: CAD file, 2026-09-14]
System_development/Pelican/structural_model/v0.3.1/Manufacturing/Male_Tail.stp
204.5 x 251.9 x 33.0 mm

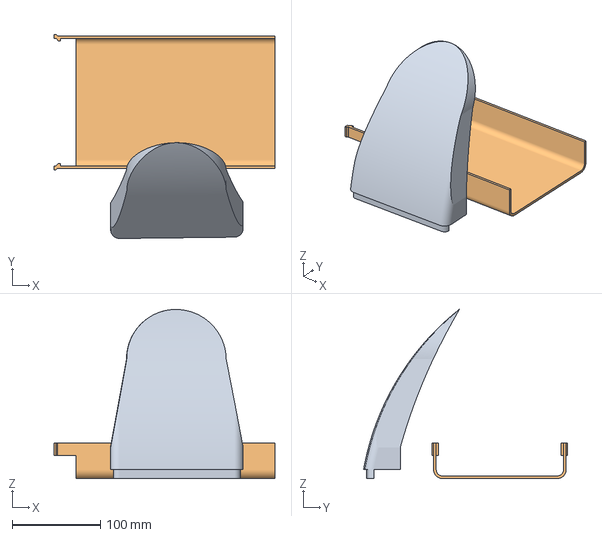
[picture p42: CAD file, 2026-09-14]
System_development/Pelican/structural_model/v0.3.1/Manufacturing/FrontCover_1.3mf
250.0 x 230.8 x 191.2 mm
FrontCover_1
FrontCover_2

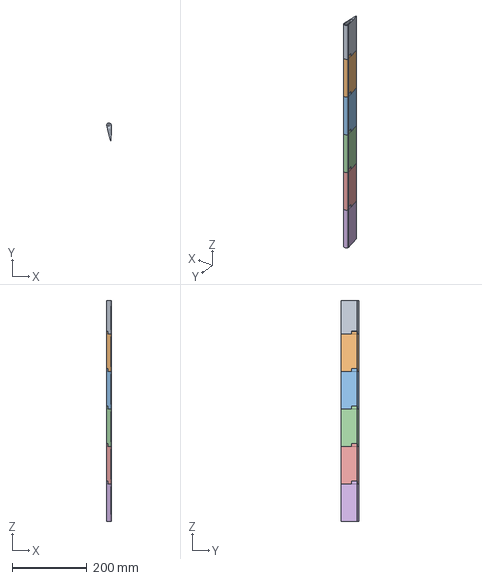
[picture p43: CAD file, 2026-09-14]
System_development/Pelican/structural_model/v0.3.1/Manufacturing/AlerionLeft_V2.stp
12.7 x 48.5 x 590.0 mm

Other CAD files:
System_development/Heron/structural_model/v0.1.0/Full_Assembly17.dwg
System_development/Heron/structural_model/v0.1.0/Full_Assembly.dwg
System_development/Heron/structural_model/v0.1.0/Fuselage_Payload17.dwg
System_development/Heron/structural_model/v0.1.0/fuselage.dwg
System_development/Heron/structural_model/v0.1.0/Avionics.ipt
System_development/Heron/structural_model/v0.1.0/Avionics1.ipt
System_development/Heron/structural_model/v0.1.0/Avionics1_MIR.ipt
System_development/Heron/structural_model/v0.1.0/Avionics_MIR.ipt
System_development/Heron/structural_model/v0.1.0/Battery.ipt
System_development/Heron/structural_model/v0.1.0/Battery1.ipt
System_development/Heron/structural_model/v0.1.0/Camera.ipt
System_development/Heron/structural_model/v0.1.0/Camera1.ipt
System_development/Heron/structural_model/v0.1.0/Comm1.ipt
System_development/Heron/structural_model/v0.1.0/Comms.ipt
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

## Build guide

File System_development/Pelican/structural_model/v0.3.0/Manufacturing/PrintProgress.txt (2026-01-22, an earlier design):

Printed
LW1
LW2
LW3
LW4
LW5
RW1
RW2
RW4
RW5
RW3
Nose and 2nd fuselage section
Wing Box
Fuselage End 

Printing
Last part for Fuselage

Reprinting 
RW2
LW2

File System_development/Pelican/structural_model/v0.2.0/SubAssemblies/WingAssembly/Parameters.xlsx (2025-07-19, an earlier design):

Weight Estimation
Name | Weight (KG)
3D Printed Components | 3.4
Extrusion | 1.825
Tplates | 0.15
 | 5.375

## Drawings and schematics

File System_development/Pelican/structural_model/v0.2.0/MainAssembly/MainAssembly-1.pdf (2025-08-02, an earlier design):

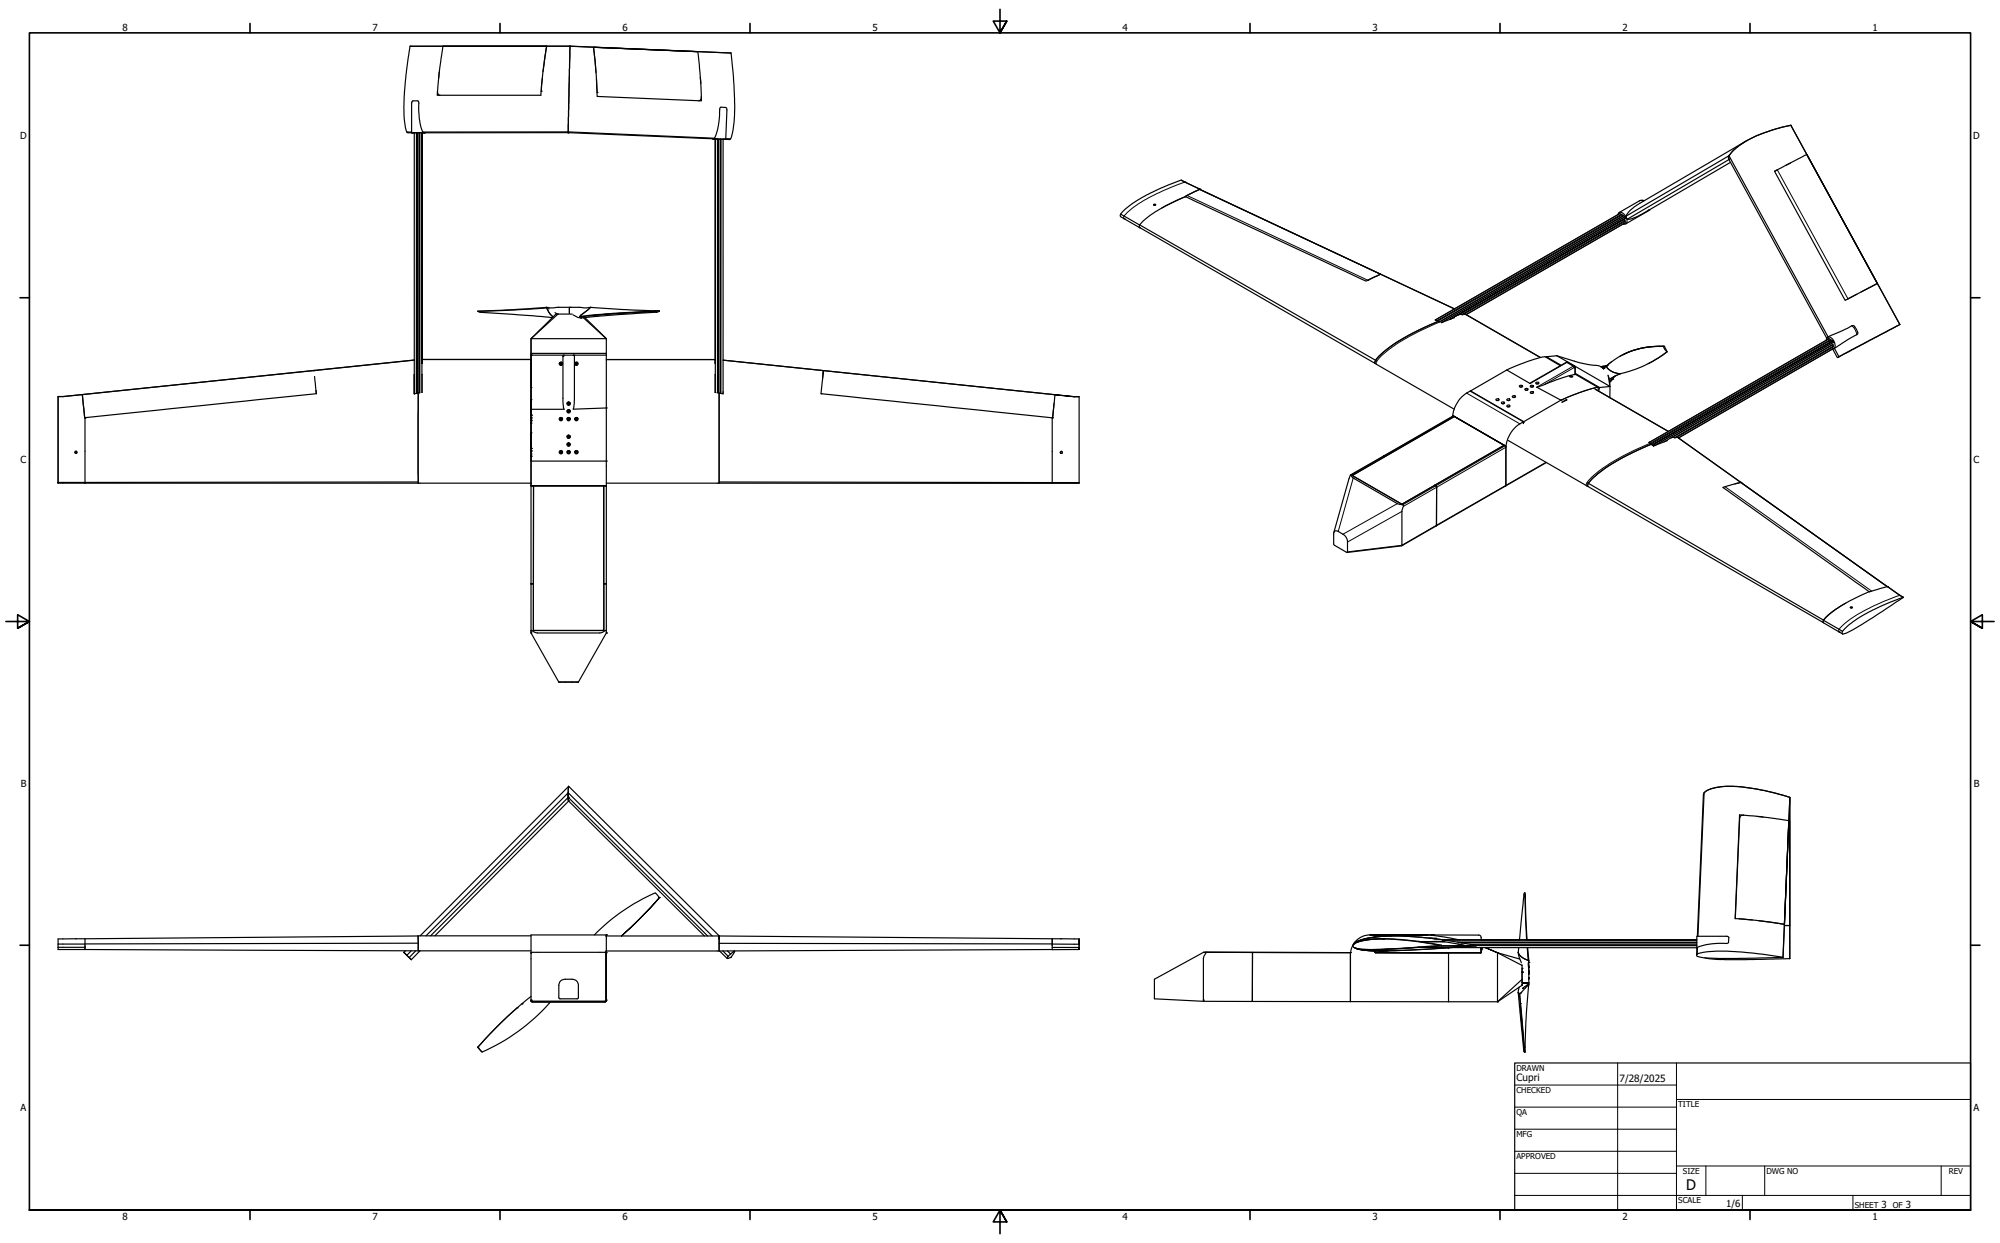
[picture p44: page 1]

DRAWN Cupri | 7/28/2025

CHECKED

MFG

APPROVED

SIZE D | DWG NO | REV

SCALE 1/6 | | SHEET 3 OF 3

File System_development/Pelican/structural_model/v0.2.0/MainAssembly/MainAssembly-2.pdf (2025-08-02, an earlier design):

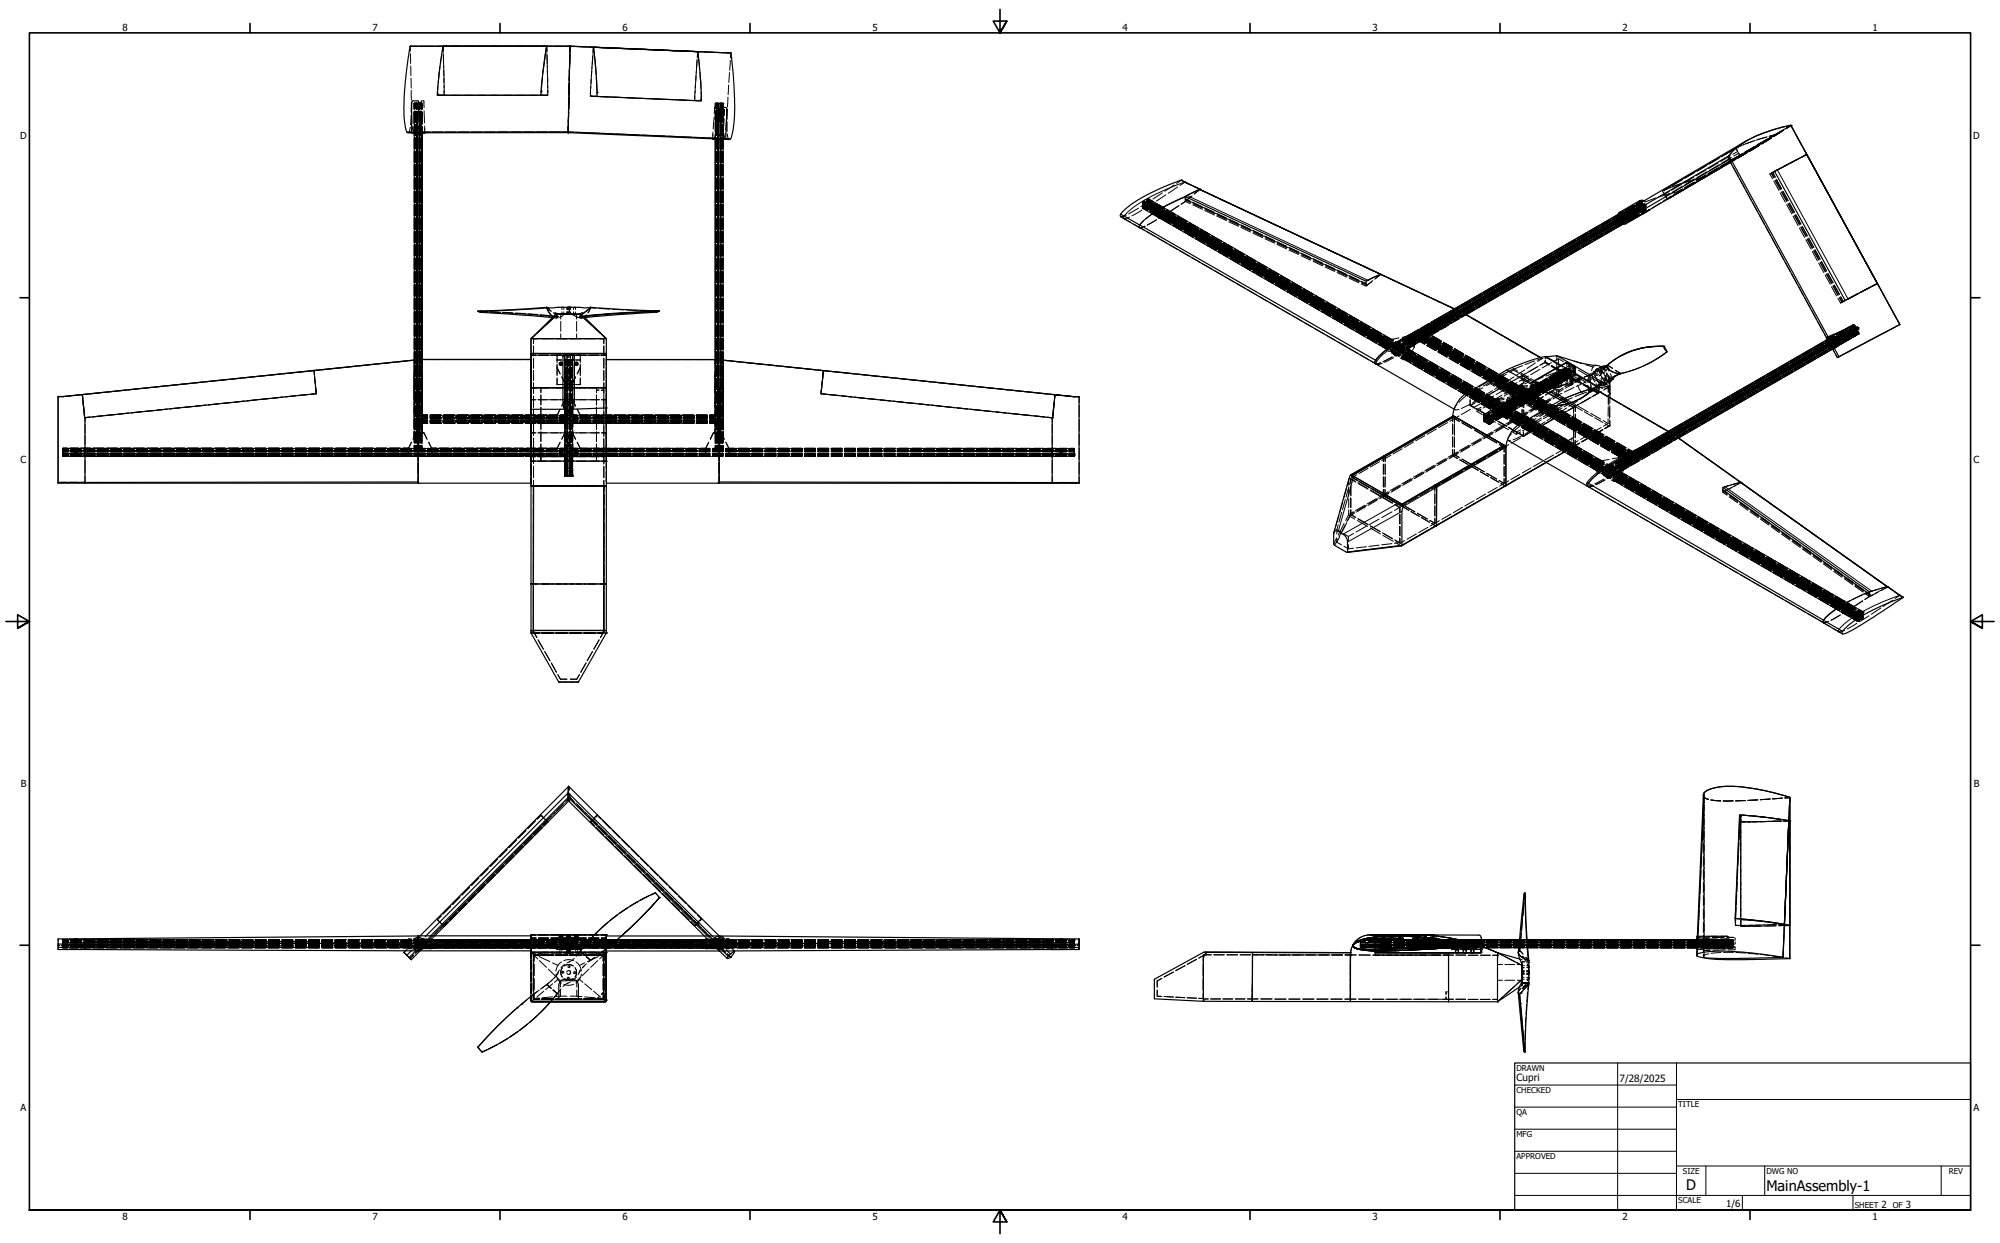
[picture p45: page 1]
SHEET 2 OF 3; DWG NO

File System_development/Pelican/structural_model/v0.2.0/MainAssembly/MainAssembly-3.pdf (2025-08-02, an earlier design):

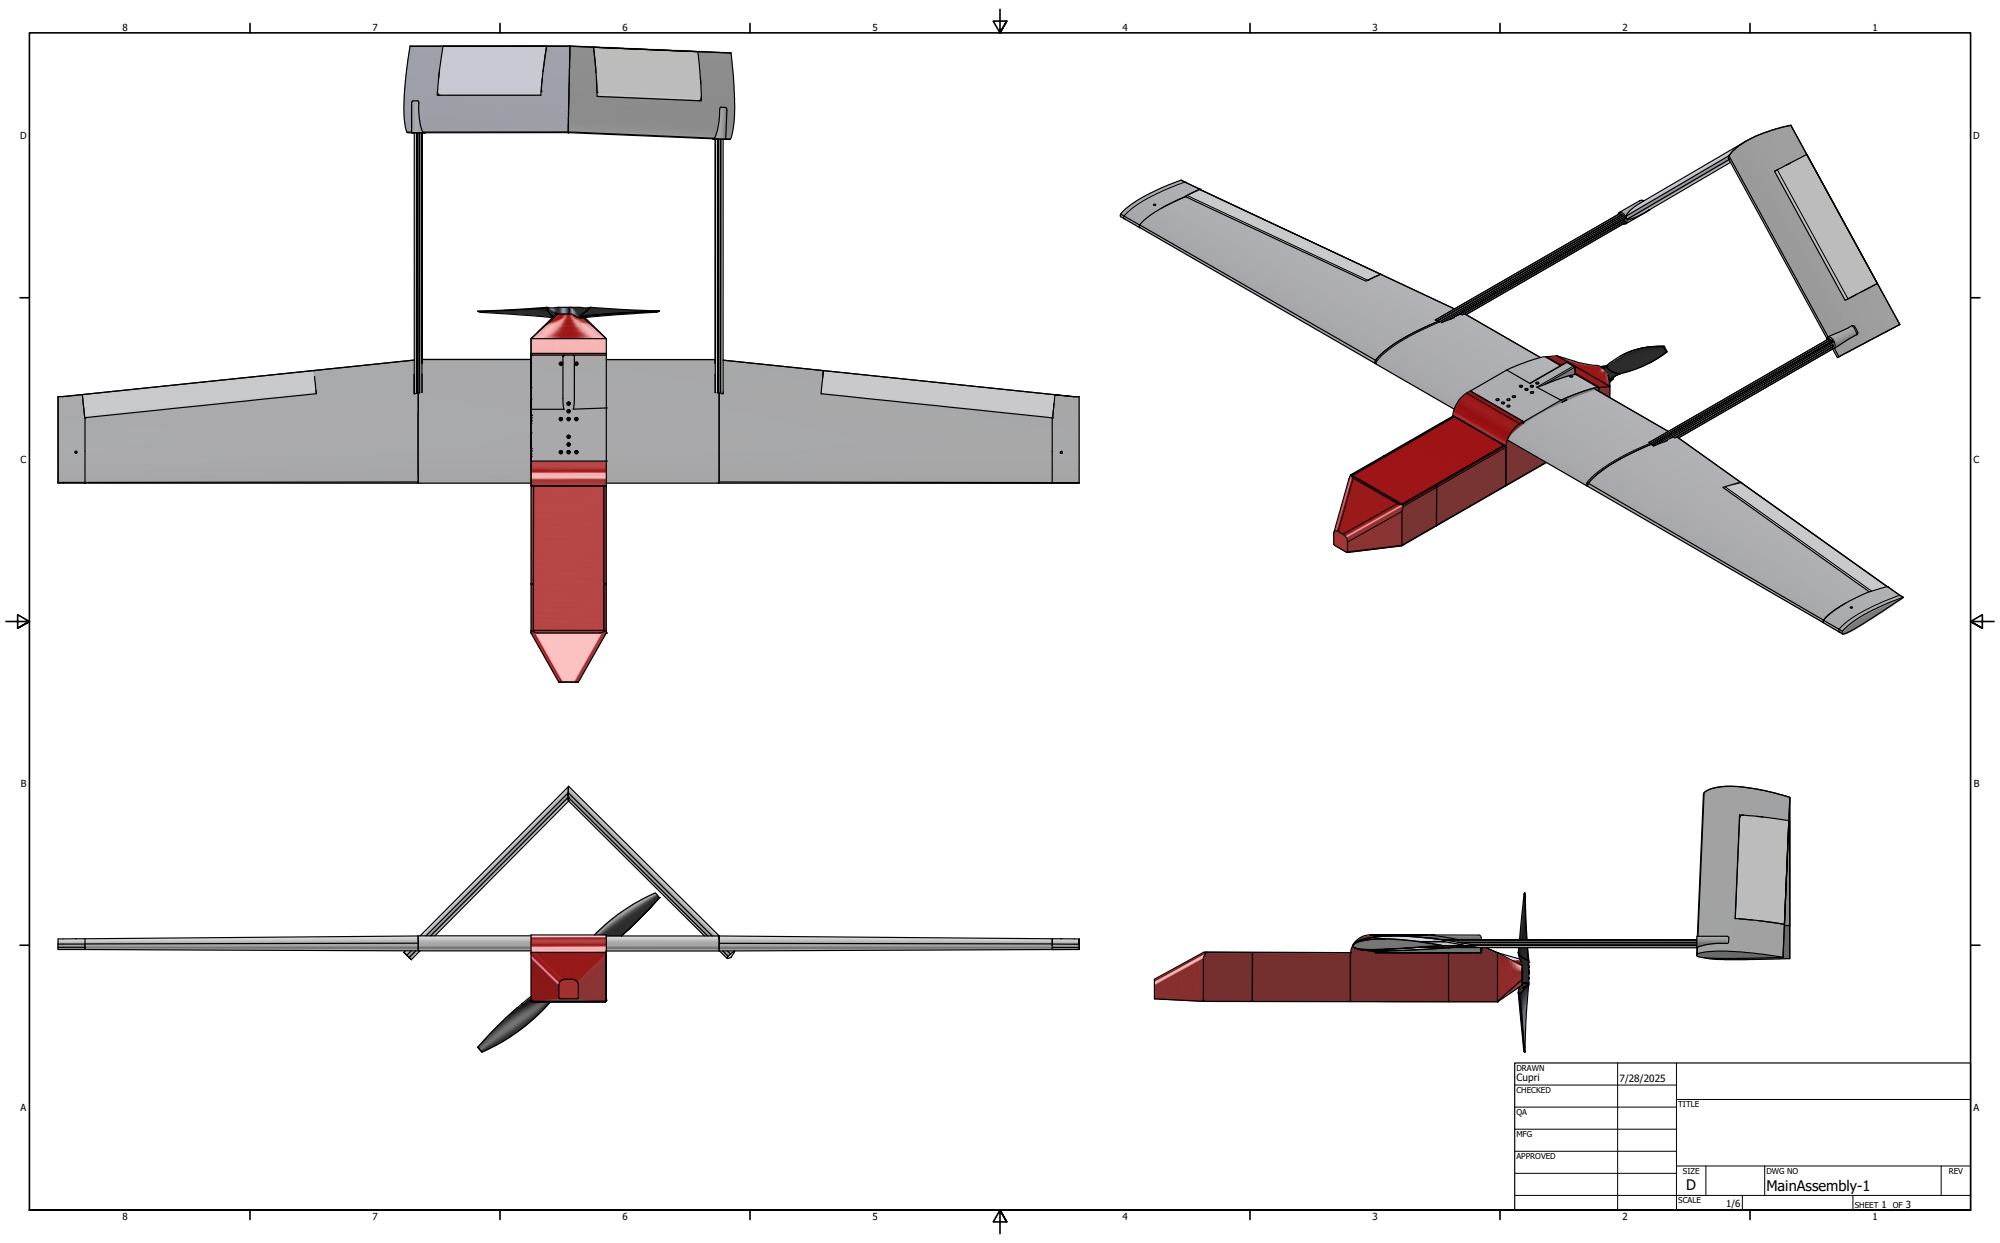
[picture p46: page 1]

DRAWN Cupri | 7/28/2025

CHECKED

MFG

APPROVED

SIZE D | DWG NO MainAssembly-1 | REV

SCALE 1/6 | | SHEET 1 OF 3

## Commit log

2025-06-10 FrameAssembly
    Added the FrameAssembly folder with the Frame assembly, and added the parts of the assembly in the FrameAssembly folder as well all under the SubAssembly folder
    [20 Series 2 Hole - 18.ipt, 20 Series 2 Hole - 18mm Slotted Inside Corner Bracket with Dual Support.step, 2020 T Plate Bracket Connectors .ipt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]
2025-06-11 Test wing print
    The test wing has a hole for the 20x20 (with a .2mm tolerance) and a hole for the DIN 6912 M4 screw where the screw head doesn't poke outside of the wing
    [TestWingSection.ipt, wingtestsection.iam]
2025-06-17 Updated test wing
    I added an extra 20x20 hole to the test wing. Then added another screw hole on the top of the test wing. I also made the the hole for the screw head a bit deeper so the screw head doesn't pop out of the wing when fully screwed. Additionally moved the screw holes to the center of the wing so it would look nicer and more organized.
    [TestWingSection.0008.ipt, wingtestsection.0004.iam]
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2025-06-24 Revert "Merge branch 'main' of https://github.com/ARTS-Laboratory/SWIFT-UAV"
    This reverts commit 80f9ccf3e957d3b2b65369b2b0b11aebb9fbf31f, reversing
    changes made to 3fb2b3669297317f653d9be0c5898ecb4c96c355.
    [20 Series 2 Hole - 18.ipt, 20 Series 2 Hole - 18mm Slotted Inside Corner Bracket with Dual Support.step, 2020 T Plate Bracket Connectors .ipt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]
2025-06-24 Reapply "Merge branch 'main' of https://github.com/ARTS-Laboratory/SWIFT-UAV"
    This reverts commit 7f71ea1c20c186fe098f32ce7f783f18926eb76a.
    [20 Series 2 Hole - 18.ipt, 20 Series 2 Hole - 18mm Slotted Inside Corner Bracket with Dual Support.step, 2020 T Plate Bracket Connectors .ipt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]
2025-06-24 Prototype new wing design
    Here in these files I have added 20x20 holes and screw holes for the wing. This is a just a prototype since I still need to add holes for the connecters, but I'm committing this so my progress doesn't get erased like it did this morning
    [MiddleWing.ipt, OuterWingLeft.ipt, OuterWingRight.ipt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]
2025-06-27 Updated wing design
    I added a hole for the T connector in the wing design, and I added a new hole for the 20x20 that comes out vertically in the frame
    [MiddleWing.0001.ipt, MiddleWing.0002.ipt, MiddleWing.0007.ipt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]
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2025-07-01 Added Tail to FrameAssembly
    [45 Degree Connector .ipt, FrameAssembly.0005.iam, FrameAssembly.0007.iam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]
2025-07-10 Updated wing design
    Here is the current wing that I have worked up too. I have moved the extrusions of the vertical 20x20 so that the bulk of the hole is in the middle wing while the right and left wings have a small am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
    [MiddleWing.ipt, OuterWingLeft.ipt, OuterWingRight.ipt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]
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2025-08-23 Corrected Fuselage File
    [Fuselage.0003.ipt, Fuselage.0004.ipt, Fuselage.ipt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]
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2025-08-29 clean up dir names
    [20 Series 2 Hole - 18.ipt, 20 Series 2 Hole - 18mm Slotted Inside Corner Bracket with Dual Support.step, 2020 T Plate Bracket Connectors .0002.ipt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]
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2025-09-17 V2.3 Fuselage Changes + Pylon
    [Fueselage.0009.ipt, Fueselage.0010.ipt, Fueselage.ipt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]
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2025-10-08 Wing tabs design V0.2.3
    [Wing Section - Copy.0002.ipt, Wing Section - inset hole.0003.ipt, Wing Section - inset hole.ipt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]
2025-10-13 Fuselage and Wing Updates V0.2.3
    [Fueselage.0014.ipt, Fueselage.0016.ipt, Fueselage.ipt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]
2025-10-13 Fixes to Assembly and Mount V0.2.3
    [Fueselage.0016.ipt, Fueselage.0017.ipt, Fueselage.ipt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]
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2025-10-16 Wing Nub Updates V0.2.3
    [MainAssembly.0035.iam, MainAssembly.0036.iam, MainAssembly.iam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]
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2025-10-24 Cover and Wingbox Updates
    [FrontCover.0004.ipt, FrontCover.0011.ipt, FrontCover.ipt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]
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2025-11-10 tail changes and powerpoint slides
    [FrontCover.0011.ipt, FrontCover.0013.ipt, FrontCover.ipt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]
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2025-12-12 Add files via upload
    Updated wing box with inverted bumps
    [WingBoxv0.2.4.stl]
2025-12-13 WingBox_V_0.2.4
    Version 0.2.4 – Remeshed wing cover; surface smoothed and outward bumps removed. Mesh is closed and validated.
    [WingBox_V0.2.4.stl]
2025-12-19 Tail and Control Surface Updates
    [MainAssembly.0051.iam, MainAssembly.0054.iam, MainAssembly.iam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]
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2026-01-14 Landing gear + Wing box nut
    [Fueselage.0036.ipt, Fueselage.0038.ipt, Fueselage.ipt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]
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2026-02-05 V3.0 + new BOM
    [2020 T Plate Bracket Connectors .0002.ipt, 2020 T Plate Bracket Connectors .ipt, 2020 T Plate Bracket Connectors .stp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]
2026-02-18 V3 updates to wingbox mounting
    [Fueselage.0039.ipt, Fueselage.0040.ipt, Fueselage.ipt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]
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2026-02-23 BOM fixes
    [2020 T Plate Bracket Connectors .0002.ipt, 2020 T Plate Bracket Connectors .ipt, 2020 T Plate Bracket Connectors .stp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]
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2026-04-01 Updated Fueselage - Front Strut Clerance
    Fueselage updated to fit new front strut connection
    [Fueselage.ipt]
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2026-04-14 Fuselage and Aileron Updates
    [AlerionLeft.0013.ipt, AlerionLeft.0015.ipt, AlerionLeft.ipt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]
2026-04-19 New Assembly and updates
    [20x20x130ExtrudedAluminum.0007.ipt, 20x20x130ExtrudedAluminum.0008.ipt, 20x20x130ExtrudedAluminum.ipt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]
2026-04-29 Updates and Fixes
    [ASPO-4525.ipt, AlerionLeft.0016.ipt, AlerionLeft.0018.ipt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]
2026-06-09 New Tail
    Made my own folder with the parts for the new tail I'm designing. I made the new tail airfoil .25 in thinner. I now need tow work on adding holes for servos, 20x20, and screws.
    [Delb_Tail_v1.iam, Delb_Tail_v1.ipt, Tail.0024.ipt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]
2026-06-09 Fixed measurements for tail
    Measured a bit wrong the first time and fixed it so the measurements should closer to the expected thickness of the new tail
    [Delb_Tail_v1.0001.ipt, Delb_Tail_v1.ipt, Tail.0025.ipt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]
2026-06-10 Updated tail
    I redid a bunch of measurements but was finally able to get a thinner tail and I am working on transferring extrusions and holes from the original tail to the new one.
    [Delb_Tail_v1.0001.ipt, Delb_Tail_v1.0002.ipt, Delb_Tail_v1.ipt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]
2026-06-11 Updated Tail again
    I added some screw hole and a place for the boom. I still have to add places for the servos dove tail mates and a bunch of plane nonsense that requires me to bend space and time to do
    [Delb_Tail_v1.0002.ipt, Delb_Tail_v1.0006.ipt, Delb_Tail_v1.ipt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]
2026-06-12 Updated Tail (again)
    Added place for servo in the tail. Need to work on some weird looking screw holes and dove tail joint next.
    [Delb_Tail_v1.0006.ipt, Delb_Tail_v1.0009.ipt, Delb_Tail_v1.ipt]
2026-06-15 updated tail again
    Added finishing touches to the airfoil without a dovetail. I added two new airfoils one male and one female side of the dovetail mate as I work on finishing the tail.
    [Delb_Tail_Female_v1.0001.ipt, Delb_Tail_Female_v1.ipt, Delb_Tail_Male_v1.ipt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]
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2026-06-17 update tail
    i forgor to push last time but I started making the dovetail
    [Delb_Tail_Female_v1.0001.ipt, Delb_Tail_Female_v1.0003.ipt, Delb_Tail_Female_v1.ipt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]
2026-06-17 Small fixes
    [20x20x130ExtrudedAluminum.ipt, MainAssembly2.0005.iam, MainAssembly2.0008.iam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]
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2026-06-19 (Problems with saving) Accurate screwholes
    [Sunselage.0004.ipt, Sunselage.ipt]
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2026-06-19 Updated dovetail
    fixed the back end of the dovetail. I have absoultly no idea how to fix the front end but I need to work on hollowing the tail now.
    [Delb_Tail_Female_v1.0004.ipt, Delb_Tail_Female_v1.0005.ipt, Delb_Tail_Female_v1.ipt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]
2026-06-22 12 spoke complacent wheel in favor of 4 inch solid wheels
    [12spoke_wheel.ipt, 4in_Wheel.ipt]
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2026-06-26 updated tail again
    I finally fixed the dovetail *confetti* now i just need to hollow out the tail for weight stuff and also test print the dovetail to make sure it fits properly
    [Delb_Tail_Female_v1.0005.ipt, Delb_Tail_Female_v1.0006.ipt, Delb_Tail_Female_v1.ipt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]
2026-06-26 Updated tail
    Started hollowing out the female part of the tail. I still need to figure out how to do the supports so we can print it out
    [Delb_Tail_Female_v1.0006.ipt, Delb_Tail_Female_v1.0007.ipt, Delb_Tail_Female_v1.ipt]
2026-06-29 Updated Tail
    Hollowed out the tail pieces and added ribs to the female part. Don't worry I'll have the male part setup by tomorrow. Just need to work on wirecoupler and tongue, then I can print out tail
    [Delb_Tail_Female_v1.0007.ipt, Delb_Tail_Female_v1.0009.ipt, Delb_Tail_Female_v1.ipt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]
